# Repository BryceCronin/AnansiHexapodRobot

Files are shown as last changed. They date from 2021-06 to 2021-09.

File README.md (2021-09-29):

# Anansi Hexapod Robot
The Anansi Hexapod Robot is a 3D-printable hexapod frame based on 24 Dynamixel MX-28 Robot Actuators. The design is radially symmetrical and offers mounting points for custom electronic components to be added.

### License
- Anansi Hexapod **Models** by Bryce Cronin (http://cronin.cloud) is licensed under a [Creative Commons Attribution 4.0 International License](https://creativecommons.org/licenses/by/4.0/ "Creative Commons Attribution 4.0 International License").

- Anansi Hexapod **Renders** © 2020 by Bryce Cronin (http://cronin.cloud) is licensed under a [Creative Commons Attribution-NonCommercial-NoDerivatives 4.0 International License](https://creativecommons.org/licenses/by-nc-nd/4.0/ "Creative Commons Attribution-NonCommercial-NoDerivatives 4.0 International License").

## Components
### Components to 3D-Print
Unless where otherwise noted, it is recommended to 3D-print these components with normal print settings. 
| Image | Component | Required | Quantity | Notes |
| --- | --- | --- | --- | ----- |
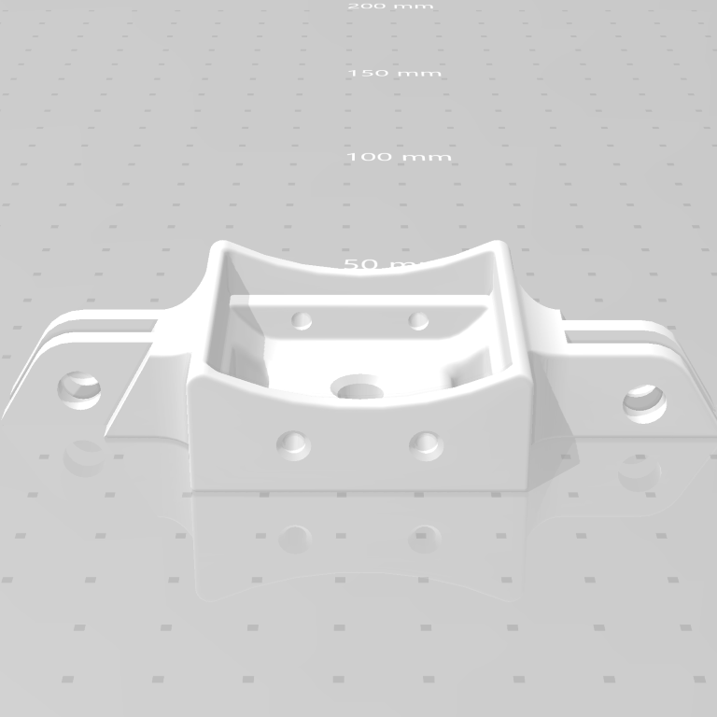
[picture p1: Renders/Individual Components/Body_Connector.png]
|  | Body_Connector  | ✔️ Required | 6 | - |
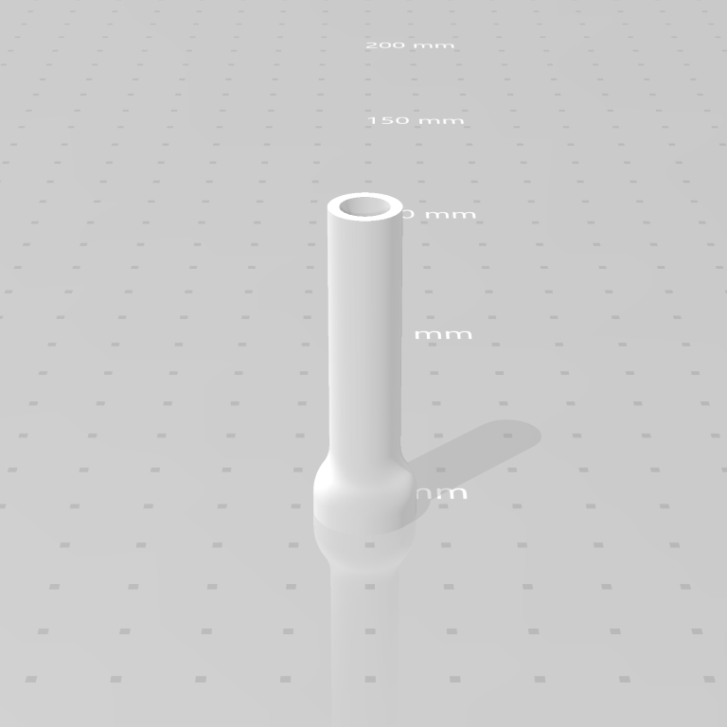
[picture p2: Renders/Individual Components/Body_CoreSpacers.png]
|  | Body_CoreSpacers | ❌ Optional  | 6 | Optional, but recommended to prevent overtightening of the *M6 60mm Bolts*. |
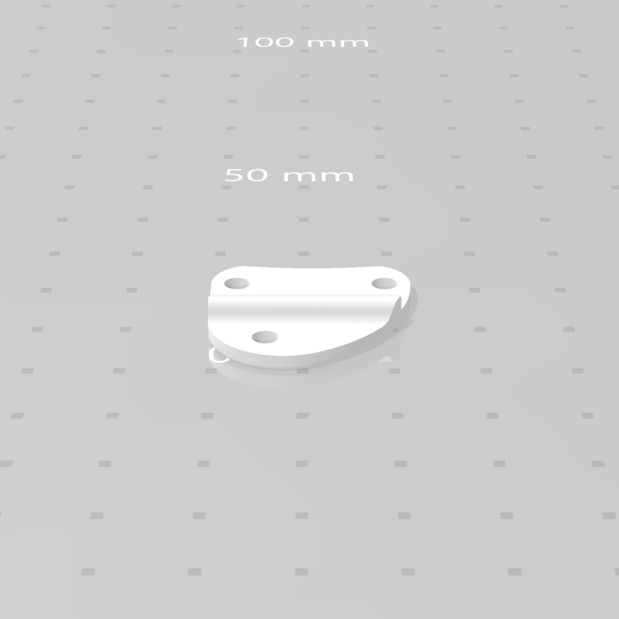
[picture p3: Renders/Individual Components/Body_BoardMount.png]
|  | Body_BoardMount | ❌ Optional  | 4 | This component can be added to the *Body_Connector* component to provide mounting points for electronics, however it is recommended to design a custom component to suit your exact needs. |
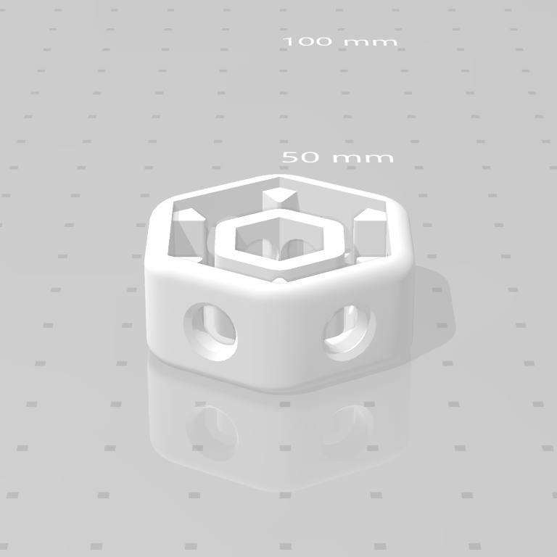
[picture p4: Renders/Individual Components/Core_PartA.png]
|  | Core_PartA  | ✔️ Required | 1 | May require high-precision 3D-print settings to allow for the *M6 Hex Nuts* to be inserted into this component. |
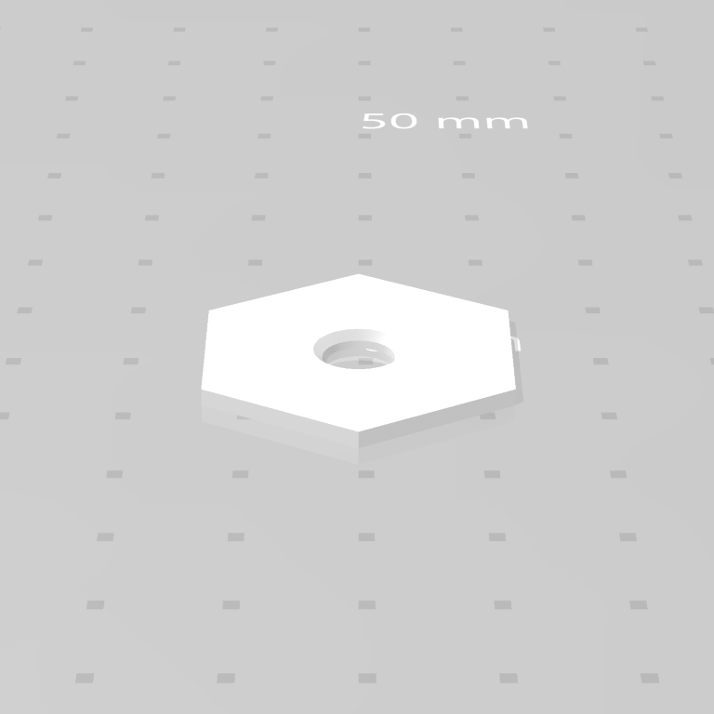
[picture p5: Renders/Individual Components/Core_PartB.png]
|  | Core_PartB | ✔️ Required | 1 | May require high-precision 3D-print settings to allow for this component to be inserted into Core_PartA.|
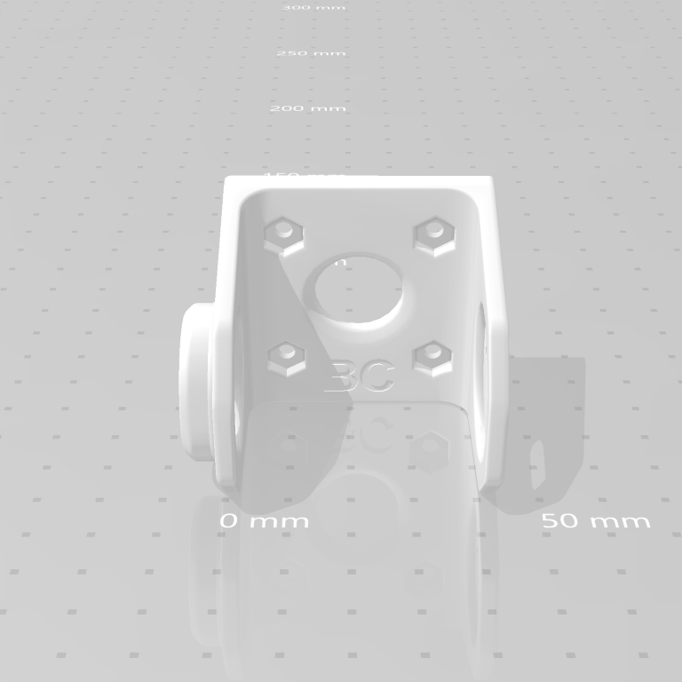
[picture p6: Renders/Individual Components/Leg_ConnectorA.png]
|  | Leg_ConnectorA  | ✔️ Required | 24 | Print this piece so that it looks like a *'U'* shape when looking from above, this will make it flexible so that motors can be inserted and removed. Alternatively, you can edit the model to extend the oval shape to the very edge so that motors can be inserted and removed without a great amount of flexibility in the printed model.  |
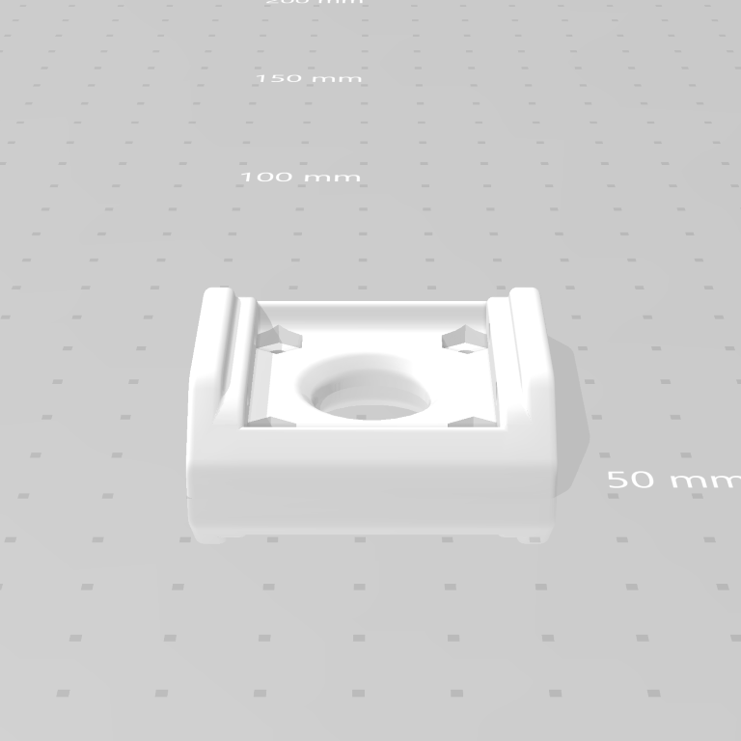
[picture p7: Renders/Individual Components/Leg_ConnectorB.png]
|  | Leg_ConnectorB  | ✔️ Required | 18 | 18 are required, but 24 are recommended if aesththetics are important to you. If you use 24, attach the extra components between the *Leg_ConnectorB* component and the *spacers* in each foot.|
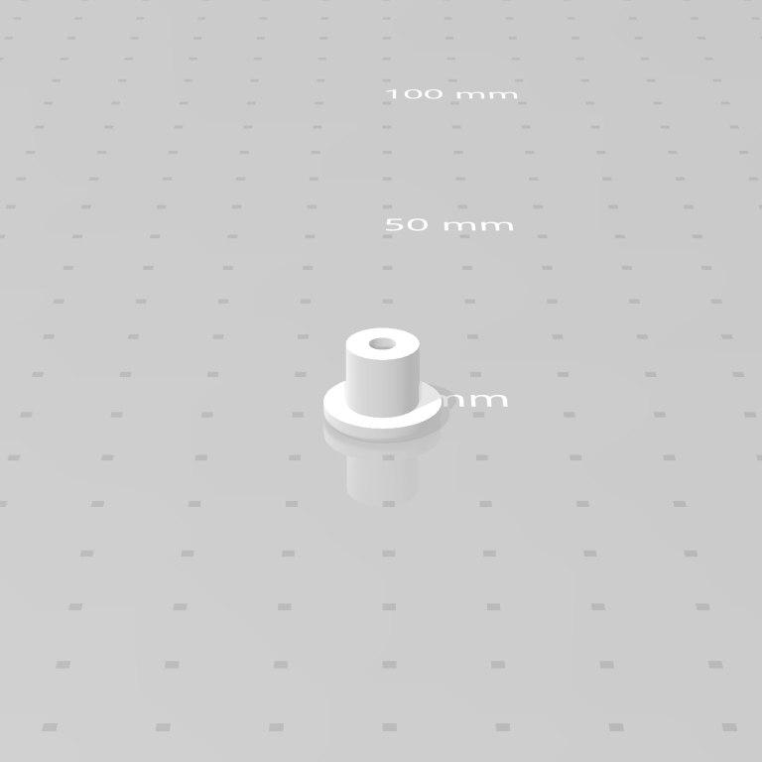
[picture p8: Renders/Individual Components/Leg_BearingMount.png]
|  | Leg_BearingMount  | ✔️ Required | 24 | - |
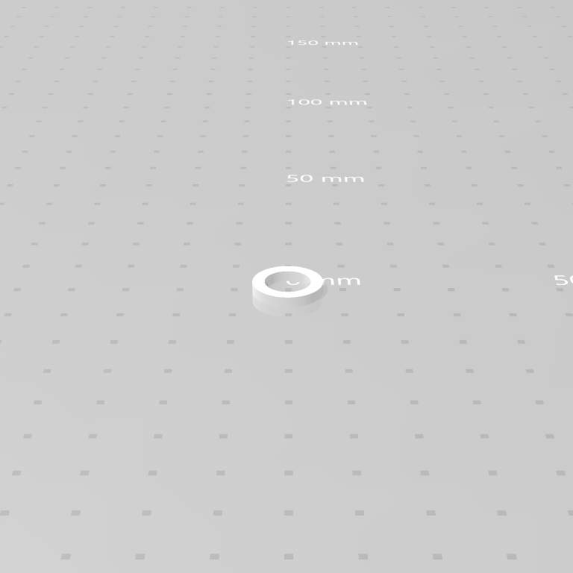
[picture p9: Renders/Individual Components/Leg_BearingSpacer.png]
|  | Leg_BearingSpacer  | ✔️ Required | 24 | Print with high precision - it should fit snuggly into the recess on the Dynamixel motor. If it doesn't fit snuggly, consider designing a custom version of this component with your 3D-printers settings in mind.|
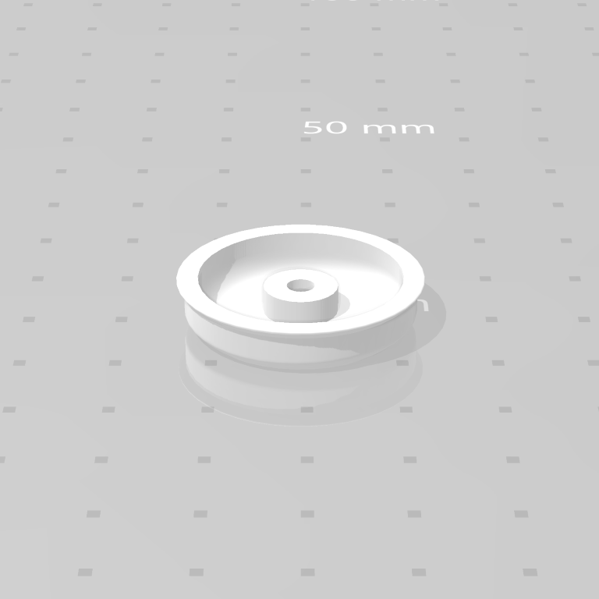
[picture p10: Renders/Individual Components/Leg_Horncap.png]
|  | Leg_HornCap  | ❌ Optional | 24 | This component is purely for aesthetic reasons. It's optional, but will make your hexapod look nice and symetrical. |
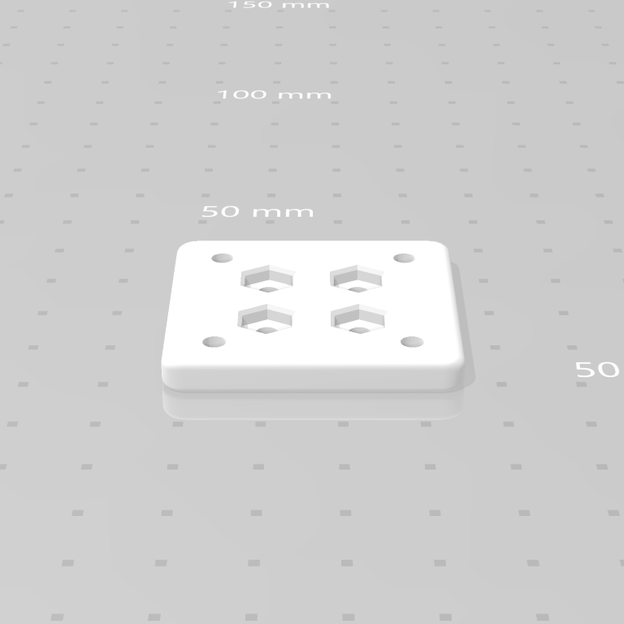
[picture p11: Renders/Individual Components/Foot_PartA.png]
|  | Foot_PartA  | ✔️ Required | 6 | - |
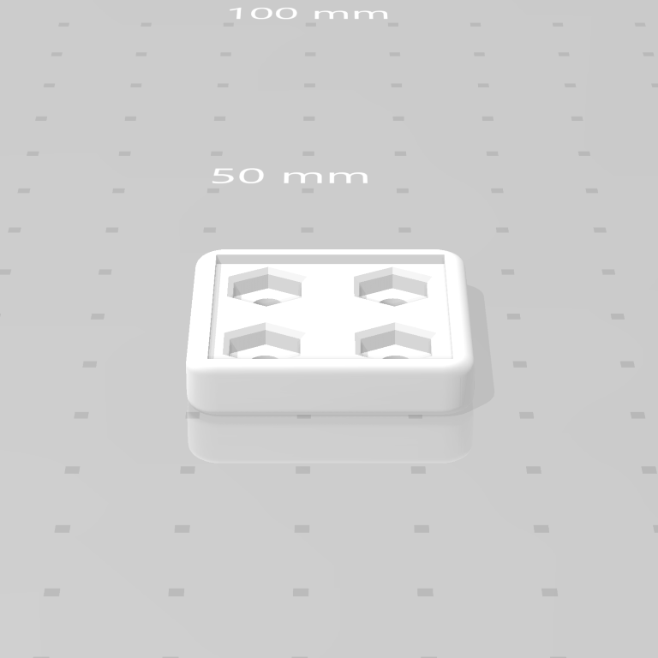
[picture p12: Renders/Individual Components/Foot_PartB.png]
|  | Foot_PartB  | ✔️ Required | 6 | - |

### Other Components
You'll need to purchase or fabricate the below components yourself. I've included links to the exact products I used for illustrative purposes only, I recommend finding similar products that are available for purchase in your region. Consider 3D-printing the *Core_PartA* and *Body_Connector* components in order to test the sizing of screws and bolts before purchasing.
| Component | Required | Quantity | Notes |
| --- | --- | --- | ----- |
| Dynamixel MX-28 Robot Actuators | ✔️ Required | 24 | These come in a few different models (T, AT, R, AR, etc). <br>*https://www.trossenrobotics.com/dynamixel-mx-28-robot-actuator.aspx*|
| 8mm x 22mm x 7mm Bearings | ✔️ Required | 24 | *https://www.ebay.com.au/itm/282588304295*|
| Rubber Feet | ❌ Optional | 6 | 20mm x 20mm so that they fit the bottom of *Foot_PartB*. <br>*https://www.jaycar.com.au/rubber-feet-large-stick-on-pk-20/p/HP0822* |
| M**3** **6**mm Screws| ✔️ Required | 168 | *https://www.jaycar.com.au/m3-x-6mm-steel-screws-pk-200/p/HP0401* |
| M**3** **10**mm Screws| ✔️ Required | 72 | *https://www.jaycar.com.au/m3-x-10mm-steel-screws-pk-200/p/HP0404* |
| M**3** **15**mm Screws| ✔️ Required | 24 | *https://www.jaycar.com.au/m3-x-15mm-steel-screws-pk-200/p/HP0407* |
| M**3** Hex Nuts | ✔️ Required | 72 |  *https://www.jaycar.com.au/m3-steel-nuts-pk-200/p/HP0426* |
| M**3** Washers | ❌ Optional | 192 | Highly recommended, but not required. These are used where the 3D-printed components are screwed into the Dyanamixel motors and the servo horns.<br>*https://www.jaycar.com.au/3mm-steel-flat-washers-pk-200/p/HP0431*|
| M**3** **10**mm Spacers | ✔️ Required | 48 | These are required for assembling the 6 feet. Alternatively, you could design and 3D-print a custom foot component that doesn't require spacers. Spacers were used so that the feet could be easily extended or shortened using different sized spacers. <br>*https://www.jaycar.com.au/m3-x-10mm-tapped-metal-spacers-pk100/p/HP0901*|
| M**6** **20**mm Bolts | ✔️ Required | 6| *https://www.bunnings.com.au/pinnacle-m6-x-20mm-yellow-zinc-hi-tensile-hex-bolt-and-nut-10-pack_p2320083*  |
| M**6** **60**mm Bolts | ✔️ Required | 6| *https://www.bunnings.com.au/pinnacle-m6-x-60mm-stainless-steel-hex-head-bolts-and-nuts-6-pack_p0087642* |
| M**6** Hex Nuts | ✔️ Required | 14 | I recommend using lock-nuts for 6 (out of the 14) of these to connect the 6 *Body_Connector* components together.<br>*https://www.bunnings.com.au/pinnacle-m6-x-60mm-stainless-steel-hex-head-bolts-and-nuts-6-pack_p0087642* |
| M**6** Washers | ❌ Optional | 18 | Recommended, but not required.<br>*https://www.bunnings.com.au/zenith-1-4-m6-zinc-plated-machine-washer-46-pack_p2420281* |
| Glue | ✔️ Required | 1 | A small amount of superglue is required for assembling the *core*.|

## Assembly Instructions
Refer to images of the completed hexapod for assistance in assembly process.
1. **3D-Print components:** 3D-print the required components. You can find advice for 3D-printing individual components in the 'notes' column in the 'Components to 3D-Print' table above.<br><br>
2. **Assemble the core:** Insert 8 *M6 Hex Nuts* into *Core_PartA*. Ensure the nuts are properly centred to the holes, then secure the nuts in place using glue. Then, glue *Core_PartB* into the cutout of *Core_PartA*.<br><br>
3. **Assemble the body:** Connect the interlocking wings of the 6 *Body_Connector* pieces so that they form a hexagon. Use 1 *M6 20mm bolt*, 2 *M6 washers*, and 1 *M6 hex nut* to connect each piece together.<br><br>
4. **Connect the body to the core:** Slide *M6 60mm bolt* through 1 *M6 washer*, then through a *Body_Connector* piece, then through a *Body_CoreSpacers* piece, then screw into the assembled core.<br><br>Repeat this for each side of the hexagon. Go slow, do not overtighten.<br><br>
5. **Prepare bearing assembly:** Insert a *Leg_BearingSpacing* into each Dynamixel motor (on the opposite side of the horn), they should fit snuggly. Then insert a *bearing* into each *Leg_ConnectorA* component, they should fit snuggly.<br><br>
6. **Attach motors:** Follow this step for each motor. Ensure the included servo horn is attached firmly to the motor, then slide it into a *Leg_ConnectorA* piece. <br><br>Next, slide an included servo horn screw through a *Leg_BearingMount* piece, then through *Leg_ConnectorA* (and the *bearing*), then through *Leg_BearingSpacer* (which is attached the the motor), then screw it into the motor.<br><br>On the other side of the motor, use the smaller included servo horn screws to screw through *Leg_ConnectorA* and into the servo horn in each of the 3 holes. If you want, you can then screw a *Leg_HornCap* on top to make it look pretty.<br><br>
7. **Leg assembly:** Now that each motor is attached to a *Leg_ConnectorA* piece, connect 6 of them to the 6 *Body_Connector* pieces using 4 *M3 15mm screws* and 4 *M3 washers* each. (This is also where you add the *Body_BoardMount* pieces if you've chosen to use them.)<br><br>Then, connect another *Leg_ConnectorA* piece (and its attached motor) at a 90 degree angle to the *Leg_ConnectorA* piece that is now attached to the body. Do this using 4 *M3 6mm screws* and 4 *M3 hex nuts*. This step might be difficult if you're using a bulky screwdriver.<br><br>Using 4 *M3 6mm screws* and 4 *M3 hex nuts*, connect 2 *Leg_ConnectorB* pieces together - repeat this 6 times. Then, attach each of these to the end of each limb using 4 *M3 10mm screws* and 4 *M3 washers*<br><br>Add another motor to the end of each limb using 4 *M3 10mm screws* and 4 *M3 washers*. Attach a *Leg_ConnectorB* piece to the *Leg_ConnectorA* piece at the end of the limb using 4 *M3 6mm screws* and 4 *M3 hex nuts*.<br><br>Attach the final motor to the end of the limb using 4 *M3 10mm screws* and 4 *M3 washers*. <br><br>
8. **Assemble the feet:** Use 8 *M3 6mm screws* and 4 *M3 10mm spacers* to attached *Foot_PartA* to *Foot_PartB*. Then, add the rubber foot to the bottom of *Foot_PartB*. Next, use 8 *M3 6mm screws* and 4 *M3 10mm spacers* to attach the foot to the end of the limb.<br><br>Repeat this step for each foot.<br><br>
9. You now have a completed hexapod. If you've had trouble following these instructions, please refer to fully assembled pictures. Errors may be present in these instructions, but it should hopefully be intuitive to figure out the solution.<br><br>Feel free to get in touch with me (Bryce Cronin) via LinkedIn if you have any questions.

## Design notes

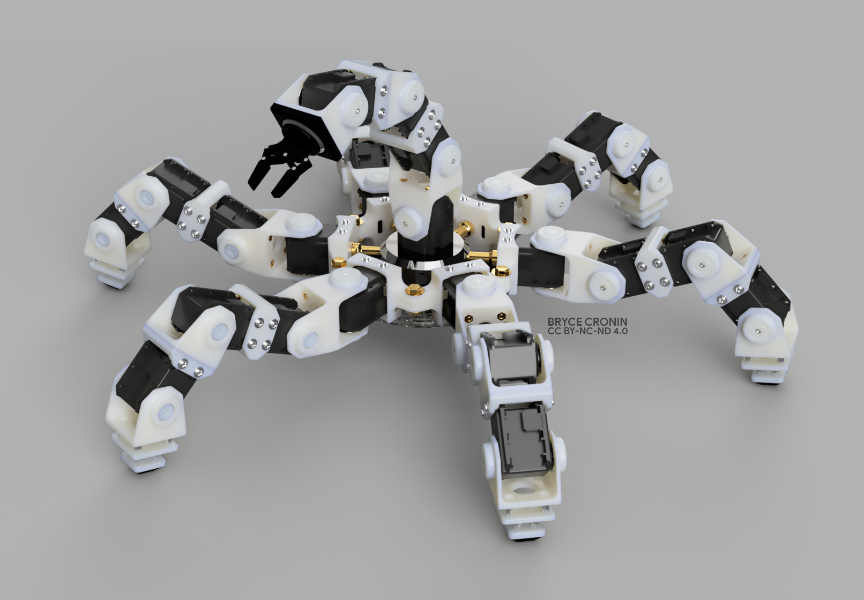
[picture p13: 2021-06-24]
Renders/Concept Upgrades/Gripper.png

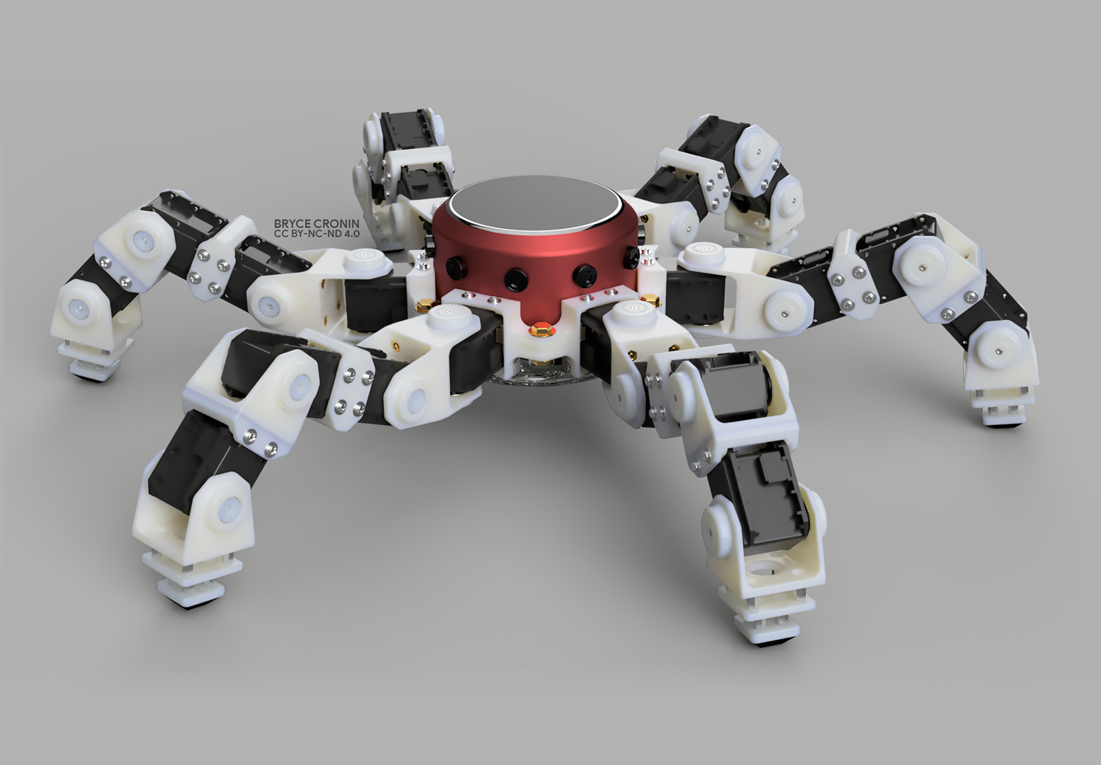
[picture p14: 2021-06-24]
Renders/Concept Upgrades/Camera.png

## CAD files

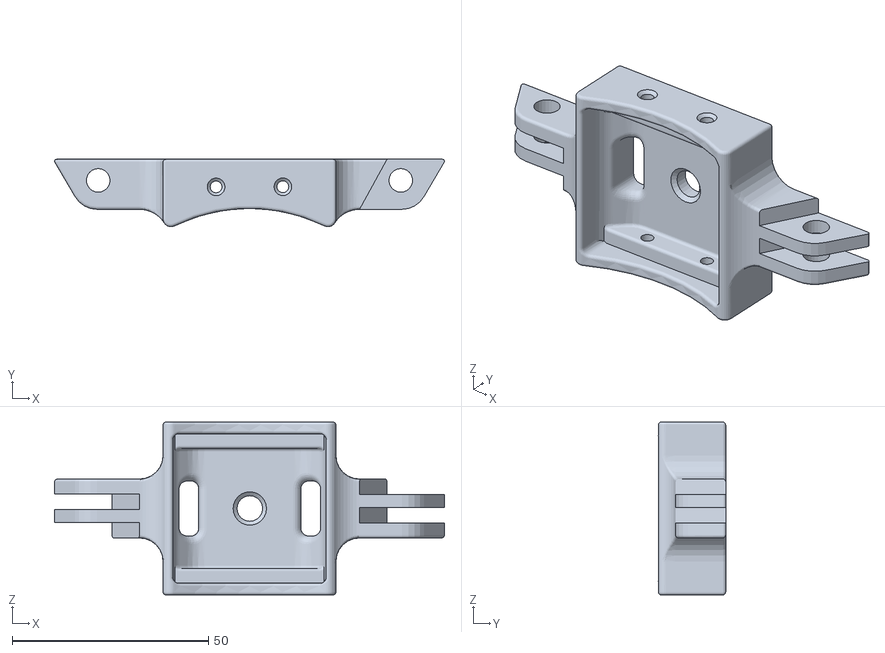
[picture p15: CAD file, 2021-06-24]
Models/Body/Body_Connector_x6.obj
99.2 x 17.2 x 44.0

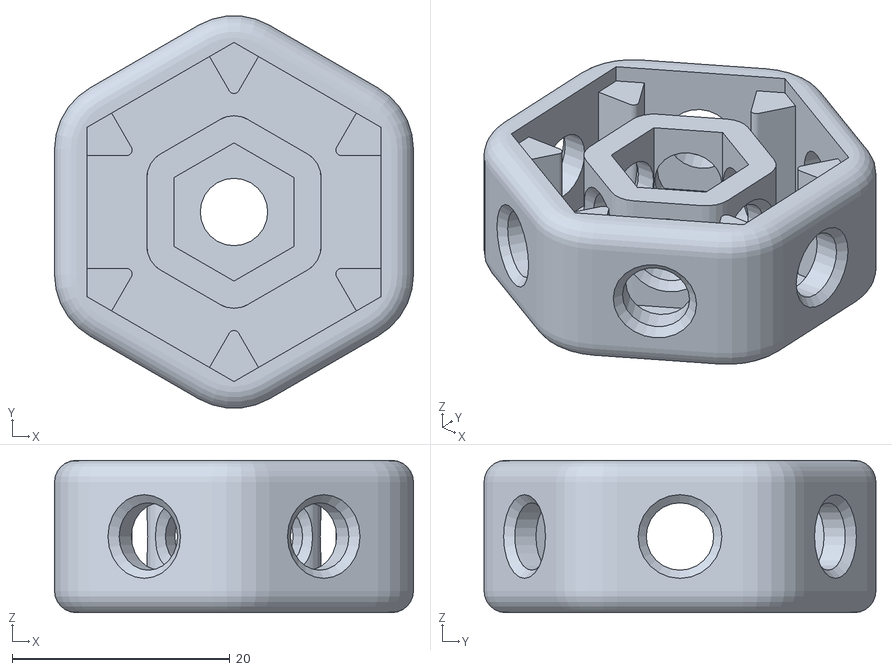
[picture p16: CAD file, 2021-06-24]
Models/Core/Core_PartA_x1.obj
33.0 x 36.0 x 14.0

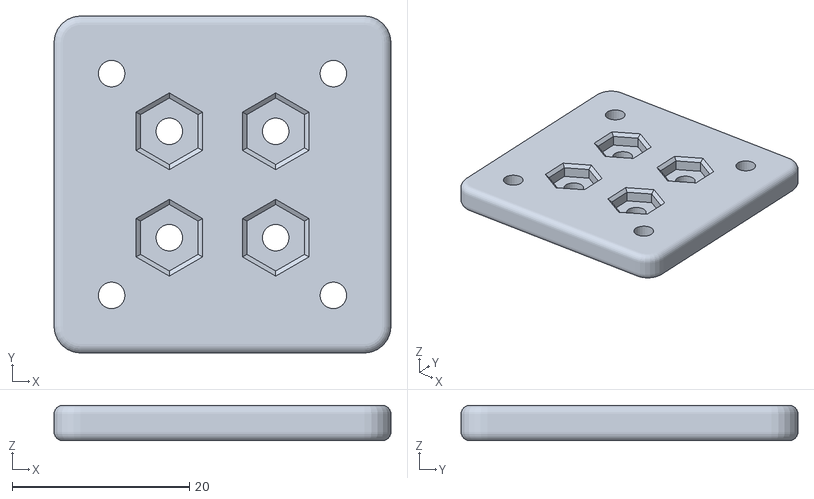
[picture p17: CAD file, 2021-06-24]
Models/Foot/Foot_PartA_x6.obj
38.0 x 38.0 x 4.00

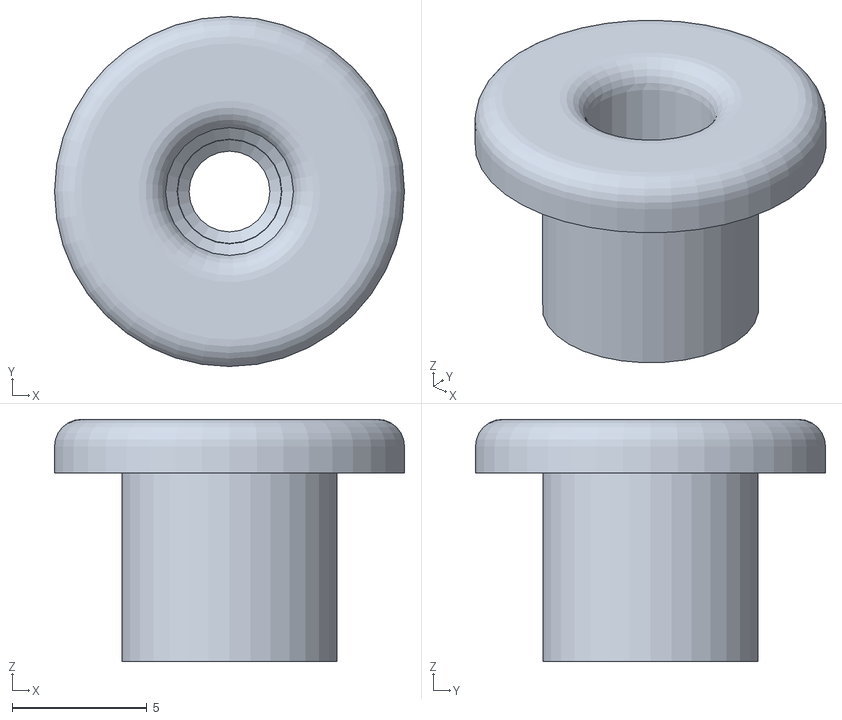
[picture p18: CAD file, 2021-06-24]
Models/Leg/Leg_BearingMount_x24.obj
13.0 x 13.0 x 9.00

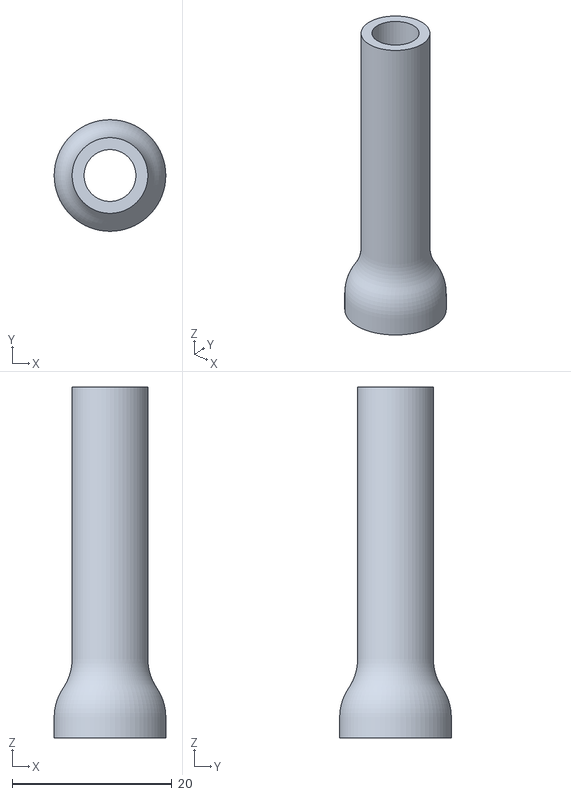
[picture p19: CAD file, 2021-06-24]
Models/Body/Body_CoreSpacers_x6_Optional.stl
14.0 x 14.0 x 44.0

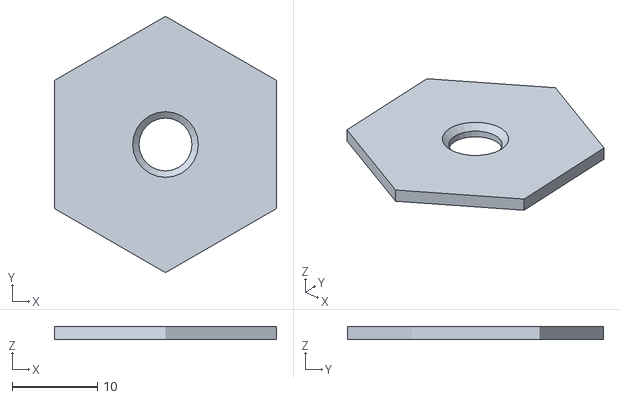
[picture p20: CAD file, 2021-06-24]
Models/Core/Core_PartB_x1.obj
26.0 x 30.0 x 1.50

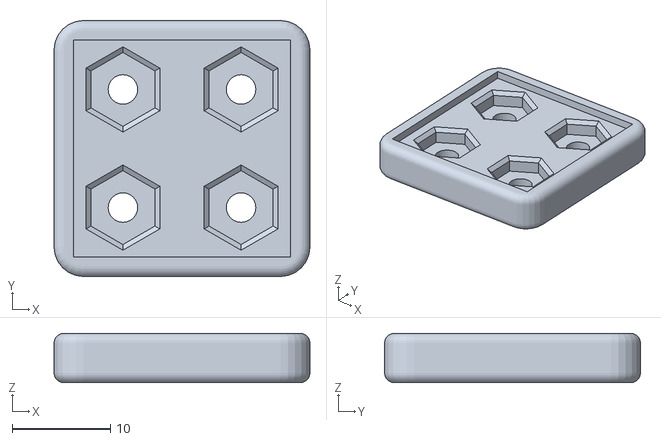
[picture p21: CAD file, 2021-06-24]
Models/Foot/Foot_PartB_x6.obj
26.0 x 26.0 x 5.00

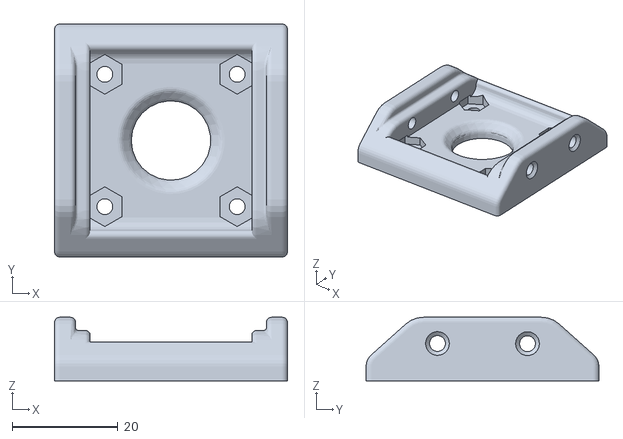
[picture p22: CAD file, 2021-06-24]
Models/Leg/Leg_ConnectorB_x24.obj
44.0 x 44.0 x 12.0

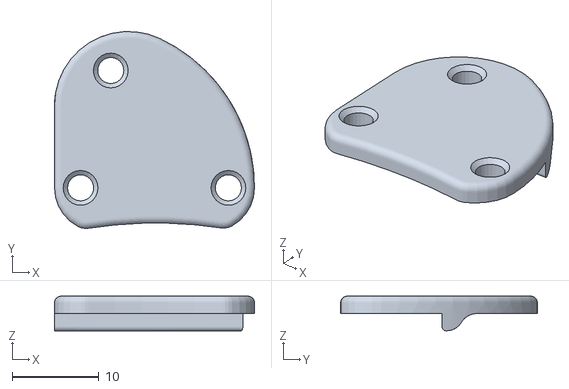
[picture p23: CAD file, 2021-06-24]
Models/Body/Body_BoardMount_x4_Optional.obj
23.0 x 22.6 x 4.00

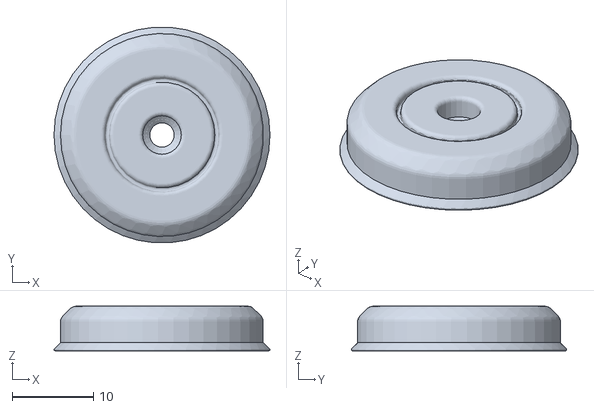
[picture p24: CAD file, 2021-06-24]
Models/Leg/Leg_Horncap_x24_Optional.obj
26.6 x 26.5 x 5.50

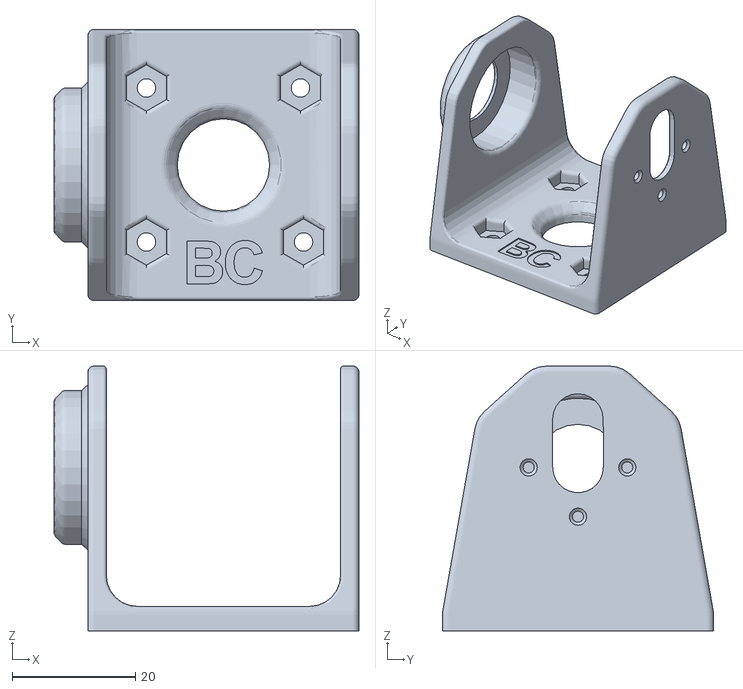
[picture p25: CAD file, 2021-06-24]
Models/Leg/Leg_ConnectorA_x24.obj
49.5 x 44.0 x 43.0

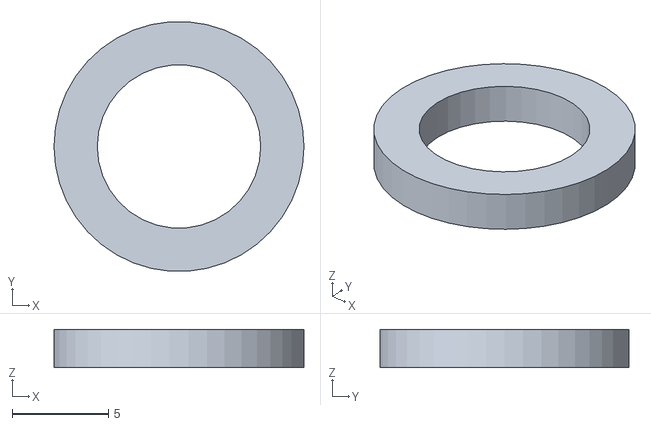
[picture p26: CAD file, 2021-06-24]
Models/Leg/Leg_BearingSpacer_x24.obj
13.0 x 13.0 x 2.00

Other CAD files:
Models/Body/Body_BoardMount_x4_Optional.f3d
Models/Body/Body_Connector_x6.f3d
Models/Body/Body_CoreSpacers_x6_Optional.f3d
Models/Core/Core_PartA_x1.f3d
Models/Core/Core_PartB_x1.f3d
Models/Foot/Foot_PartA_x6.f3d
Models/Foot/Foot_PartB_x6.f3d
Models/Leg/Leg_BearingMount_x24.f3d
Models/Leg/Leg_ConnectorA_x24.f3d
Models/Leg/Leg_ConnectorB_x24.f3d
Models/Leg/Leg_Horncap_x24_Optional.f3d

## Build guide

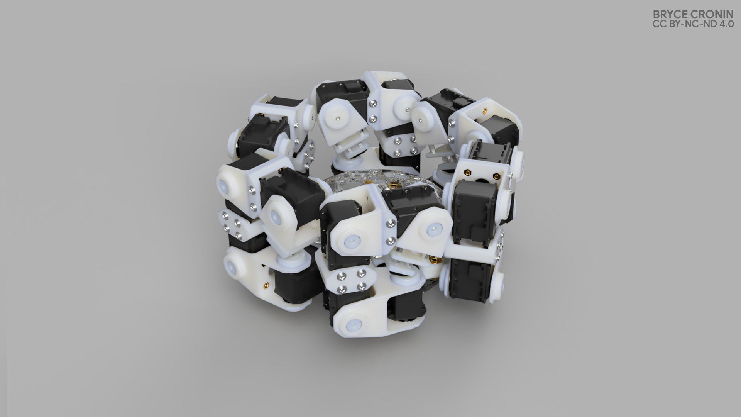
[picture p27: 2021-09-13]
Renders/Assembled Hexapod/FoldingSequence_1_Folded.jpg

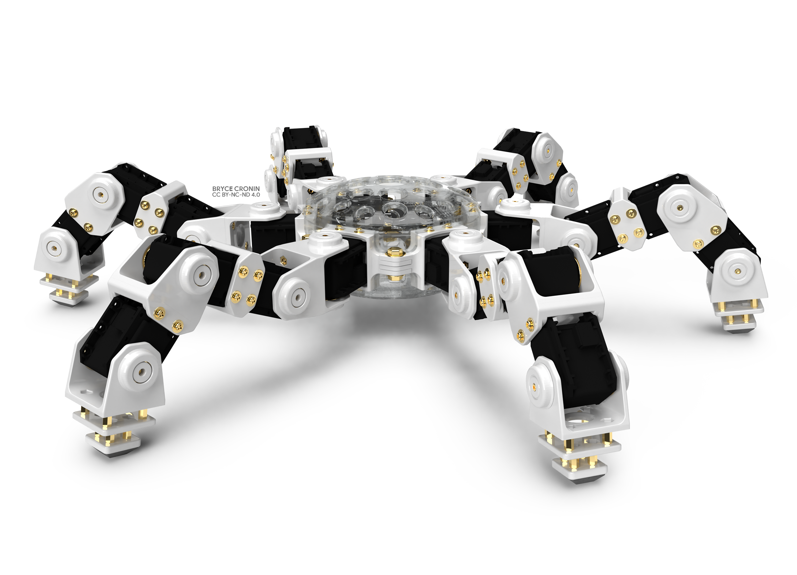
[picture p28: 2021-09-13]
Renders/Assembled Hexapod/AnansiHexapodRobot_3.png

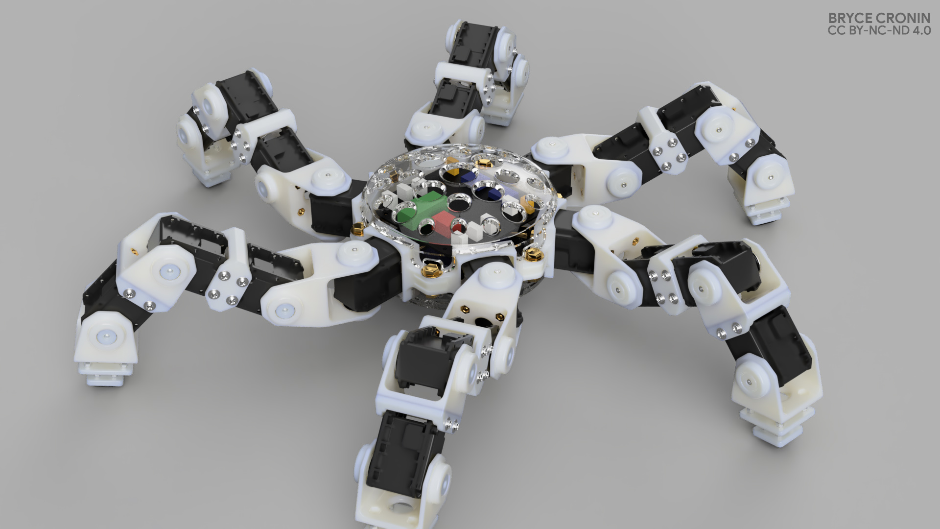
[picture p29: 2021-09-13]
Renders/Assembled Hexapod/FoldingSequence_3_Standing.jpg

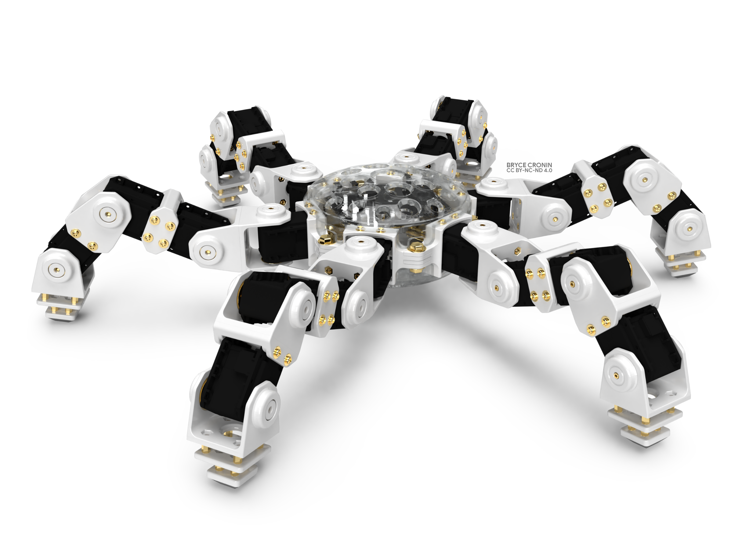
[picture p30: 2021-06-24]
Renders/Assembled Hexapod/AnansiHexapodRobot_1.png
